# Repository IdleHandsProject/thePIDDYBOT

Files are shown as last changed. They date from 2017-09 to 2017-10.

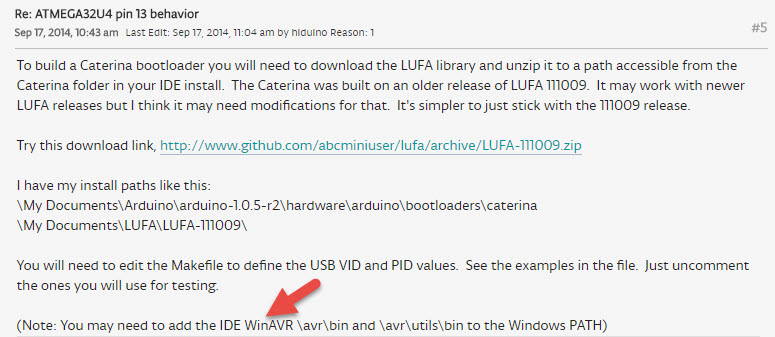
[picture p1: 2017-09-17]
PIDDYBOT_V1_32U4/bootloader/WinAVR.jpg

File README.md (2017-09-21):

# thePIDDYBOT
PIDDYBOT is an Open Source Balancing Robot with the aim of teaching PID control.

Check out the Video:

PIDDYBOT on YouTube (https://youtu.be/eyG5GFpSRSM)

Do not populate F1 or D6

**I somehow lost the original EagleCAD files for the PIDDYBOT. I still have the .BRD file, but no schem. I have plans to update the design with the SAMD21 instead of the Atmel, and it will be done in KiCad not Eagle. Stay Tuned**

There is an instructables on building the PIDDYBOT which contains the parts needed:
https://www.instructables.com/id/PIDDYBOT-DIY-Arduino-Balancing-Robot/

The FindChips(BOM):
https://www.findchips.com/org/10-open-hardware/list/46854-the-piddybot-encoders?sort=created&order=desc

HaD.io: https://hackaday.io/project/27330-the-piddybot

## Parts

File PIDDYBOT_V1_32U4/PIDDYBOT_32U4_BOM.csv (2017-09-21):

Digi-Key Part Number | Manufacturer | Manufacturer Part Number | Customer Reference | Quantity 1 | Quantity 2 | Quantity 3 | Mfg Std Lead Time | Description | Comments | RoHS Status | Lead Free Status | REACH Status
ATMEGA32U4-AURCT-ND | MICROCHIP TECHNOLOGY (VA) | ATMEGA32U4-AUR | U$1 | 1 | 0 | 0 | 14 Weeks | IC MCU 8BIT 32KB FLASH 44TQFP | Alternate Packaging Exists | RoHS Compliant | Lead free | Unaffected Jan-2017
609-3210-ND | AMPHENOL FCI | 67996-206HLF | JP5 | 1 | 0 | 0 | 8 Weeks | CONN HEADER 6POS .100 STR 15AU |  | RoHS Compliant | Lead free | Not Available
490-1459-1-ND | MURATA ELECTRONICS (VA) | GRM1885C1H222JA01D | C13 | 1 | 0 | 0 | 15 Weeks | CAP CER 2200PF 50V C0G/NP0 0603 | Alternate Packaging Exists | RoHS Compliant | Lead free | Unaffected Jun-2016
P1.0MGCT-ND | PANASONIC ELECTRONIC COMPONENTS (VA) | ERJ-3GEYJ105V | R1 | 1 | 0 | 0 | 43 Weeks | RES SMD 1M OHM 5% 1/10W 0603 | Alternate Packaging Exists | RoHS Compliant | Lead free | Unaffected Jan-2017
490-3297-1-ND | MURATA ELECTRONICS (VA) | GRM188R60J475KE19D | C3, C6 | 2 | 0 | 0 | 15 Weeks | CAP CER 4.7UF 6.3V X5R 0603 | Alternate Packaging Exists | RoHS Compliant | Lead free | Unaffected Jun-2016
740-1038-ND | MICROCHIP TECHNOLOGY | RN42-I/RM | U5 | 1 | 0 | 0 | 14 Weeks | RF TXRX MOD BLUETOOTH TRACE ANT | No delivery date available | RoHS Compliant | Lead free | Unaffected Jan-2017
490-1195-1-ND | MURATA ELECTRONICS (VA) | CSTCE8M00G55-R0 | Y1 | 1 | 0 | 0 | 9 Weeks | CER RES 8.0000MHZ 33PF SMD | Alternate Packaging Exists | RoHS Compliant | Lead free | Affected Jun-2016
311-2.00KHRCT-ND | YAGEO (VA) | RC0603FR-072KL | R4 | 1 | 0 | 0 | 16 Weeks | RES SMD 2K OHM 1% 1/10W 0603 | Alternate Packaging Exists | RoHS Compliant | Lead free | Unaffected Jan-2017
160-1446-1-ND | LITE-ON INC (VA) | LTST-C191KGKT | D1, D2 | 2 | 0 | 0 | 14 Weeks | LED GREEN CLEAR 0603 SMD | Alternate Packaging Exists | RoHS Compliant | Lead free | Unaffected Dec-2015
490-1512-1-ND | MURATA ELECTRONICS (VA) | GRM188R71H103KA01D | C16 | 1 | 0 | 0 | 39 Weeks | CAP CER 10000PF 50V X7R 0603 | Alternate Packaging Exists | RoHS Compliant | Lead free | Unaffected Jun-2016
576-1281-1-ND | MICROCHIP TECHNOLOGY (VA) | MIC5219-3.3YM5-TR | U6 | 1 | 0 | 0 | 7 Weeks | IC REG LINEAR 3.3V 500MA SOT23-5 | Alternate Packaging Exists | RoHS Compliant | Lead free | Unaffected Jan-2017
160-1447-1-ND | LITE-ON INC (VA) | LTST-C191KRKT | D11, D6 | 2 | 0 | 0 | 14 Weeks | LED RED CLEAR 0603 SMD | Alternate Packaging Exists | RoHS Compliant | Lead free | Unaffected Dec-2015
CKN9104CT-ND | C&K (VA) | PTS525SM15SMTR2 LFS | S1 | 1 | 0 | 0 | 16 Weeks | SWITCH TACTILE SPST-NO 0.02A 15V | Alternate Packaging Exists | RoHS Compliant | Lead free | Unaffected Jan-2017
1428-1007-1-ND | TDK INVENSENSE (VA) | MPU-6050 | U1 | 1 | 0 | 0 | 16 Weeks | IMU ACCEL/GYRO 3-AXIS I2C 24QFN | No delivery date available | RoHS Compliant | Lead free | Unaffected Jun-2016
MCP73831T-2ACI/OTCT-ND | MICROCHIP TECHNOLOGY (VA) | MCP73831T-2ACI/OT | U2 | 1 | 0 | 0 | 6 Weeks | IC CONTROLLR LI-ION 4.2V SOT23-5 | Alternate Packaging Exists | RoHS Compliant | Lead free | Unaffected Jan-2017
587-1242-1-ND | TAIYO YUDEN (VA) | LMK107B7105KA-T | C10, C22, C23 | 3 | 0 | 0 | 19 Weeks | CAP CER 1UF 10V X7R 0603 | Alternate Packaging Exists | RoHS Compliant | Lead free | Not Available
P3C3103-ND | PANASONIC ELECTRONIC COMPONENTS | EVU-F2AF30B14 | U$16,U$17,U$18 | 3 | 0 | 0 | 15 Weeks | POT 10K OHM 1/20W LINEAR |  | RoHS Compliant | Lead free | Not Available
160-1434-1-ND | LITE-ON INC (VA) | LTST-C190KFKT | D5,D3 | 2 | 0 | 0 | 14 Weeks | LED ORANGE CLEAR 0603 SMD | No delivery date available | RoHS Compliant | Lead free | Unaffected Dec-2015
609-4613-1-ND | AMPHENOL FCI (VA) | 10118192-0001LF | X2 | 1 | 0 | 0 | 12 Weeks | CONN USB MICRO B RECPT SMT R/A | Alternate Packaging Exists | RoHS Compliant | Lead free | Not Available
A100043-ND | TE CONNECTIVITY AMP | 440055-2 | CN2 | 1 | 0 | 0 | 13 Weeks | CONN HEADER 2POS R/A 2MM T/H |  | RoHS Compliant | Lead free | Not Available
455-1792-1-ND | JST SALES AMERICA INC (VA) | BM06B-SRSS-TB(LF)(SN) | JP3,JP4 | 2 | 0 | 0 | 14 Weeks | CONN HEADER SH 6POS TOP 1MM TIN | Alternate Packaging Exists | RoHS Compliant | Lead free | Not Available
311-1343-1-ND | YAGEO (VA) | CC0603ZRY5V9BB104 | C9, C11, C12, C14, C17, C18,C8 | 7 | 0 | 0 | 16 Weeks | CAP CER 0.1UF 50V Y5V 0603 | Alternate Packaging Exists | RoHS Compliant | Lead free | Unaffected Jan-2017
311-1.0KGRCT-ND | YAGEO (VA) | RC0603JR-071KL | R5,R2, R7, R8, R12, R21 | 6 | 0 | 0 | 16 Weeks | RES SMD 1K OHM 5% 1/10W 0603 | Alternate Packaging Exists | RoHS Compliant | Lead free | Unaffected Jan-2017
311-10KGRCT-ND | YAGEO (VA) | RC0603JR-0710KL | R6, R22, R10, R11 | 4 | 0 | 0 | 16 Weeks | RES SMD 10K OHM 5% 1/10W 0603 | Alternate Packaging Exists | RoHS Compliant | Lead free | Unaffected Jan-2017
609-3461-ND | AMPHENOL FCI | 68000-103HLF | S4 | 1 | 0 | 0 | 8 Weeks | BERGSTIK II .100" SR STRAIGHT |  | RoHS Compliant | Lead free | Not Available
P0.0JCT-ND | PANASONIC ELECTRONIC COMPONENTS (VA) | ERJ-2GE0R00X | L2 | 1 | 0 | 0 | 43 Weeks | RES SMD 0 OHM JUMPER 1/10W 0402 | Alternate Packaging Exists | RoHS Compliant | Lead free | Unaffected Jun-2016
296-30391-1-ND | TEXAS INSTRUMENTS (VA) | DRV8835DSSR | U$2 | 1 | 0 | 0 | 10 Weeks | IC MOTOR DRIVER PAR 12WSON | Alternate Packaging Exists | RoHS Compliant | Lead free | Unaffected Jun-2016
311-1376-1-ND | YAGEO (VA) | CC1206ZKY5V7BB106 | C7,C15, C5 | 3 | 0 | 0 | 15 Weeks | CAP CER 10UF 16V Y5V 1206 | Alternate Packaging Exists | RoHS Compliant | Lead free | Unaffected Jan-2017
311-22GRCT-ND | YAGEO (VA) | RC0603JR-0722RL | R9, R13 | 2 | 0 | 0 | 16 Weeks | RES SMD 22 OHM 5% 1/10W 0603 | Alternate Packaging Exists | RoHS Compliant | Lead free | Unaffected Jan-2017
311-470KGRCT-ND | YAGEO (VA) | RC0603JR-07470KL | R3 | 1 | 0 | 0 | 16 Weeks | RES SMD 470K OHM 5% 1/10W 0603 | Alternate Packaging Exists | RoHS Compliant | Lead free | Unaffected Jan-2017

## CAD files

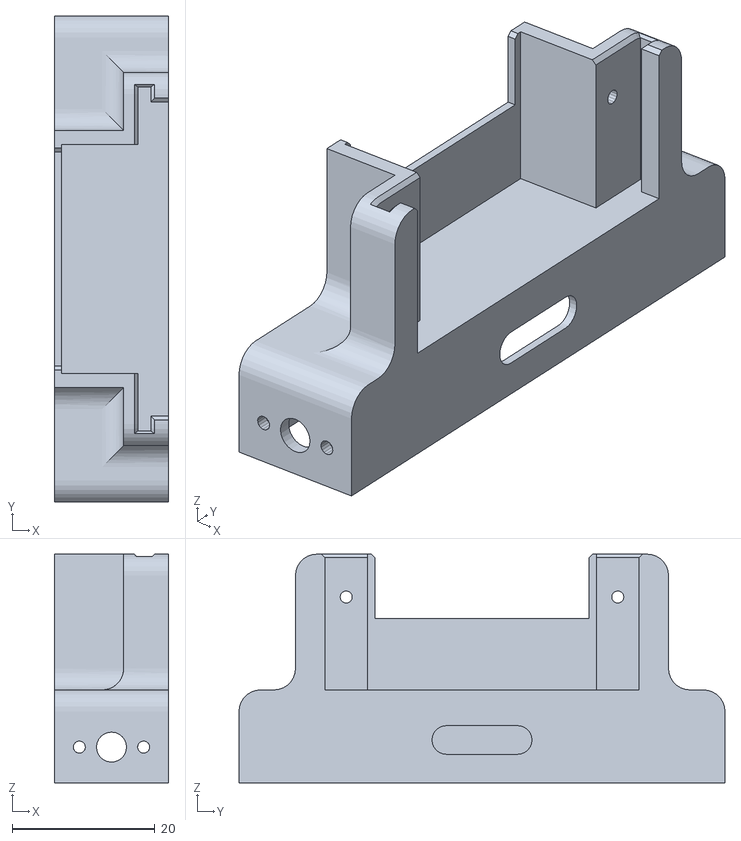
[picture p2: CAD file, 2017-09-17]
body/PIDDYBody_small_motor_lightweight.stl
16.0 x 68.0 x 32.0

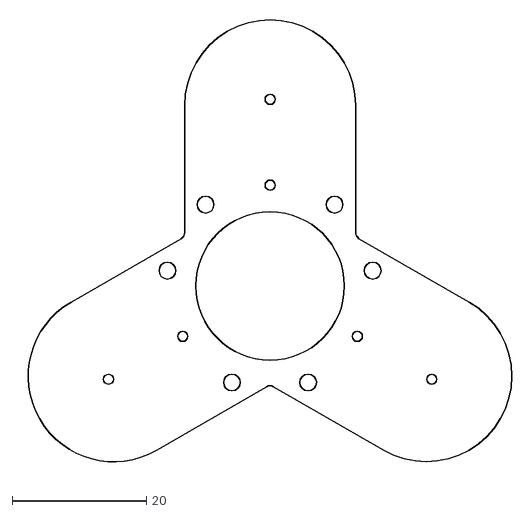
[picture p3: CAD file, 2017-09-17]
latch_encoder/PCB/Body.dxf
73.8 x 68.1

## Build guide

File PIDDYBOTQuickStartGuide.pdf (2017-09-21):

# PIDDYBOT Quick Start Guide

## For PIDDYBOT_32U4_V11 Firmware

Idle Hands Development

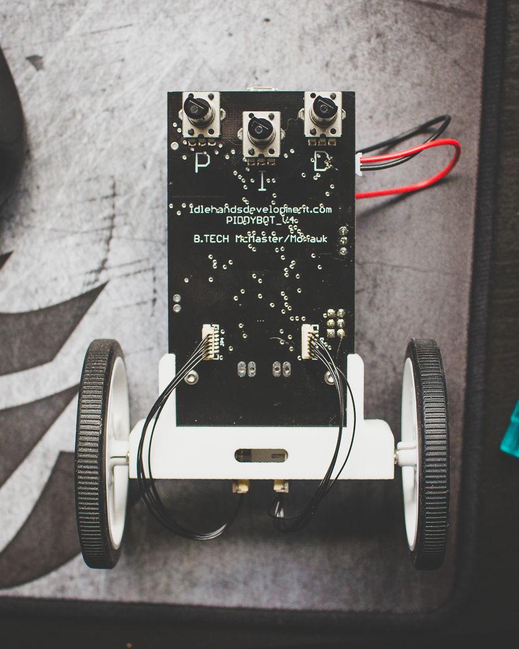
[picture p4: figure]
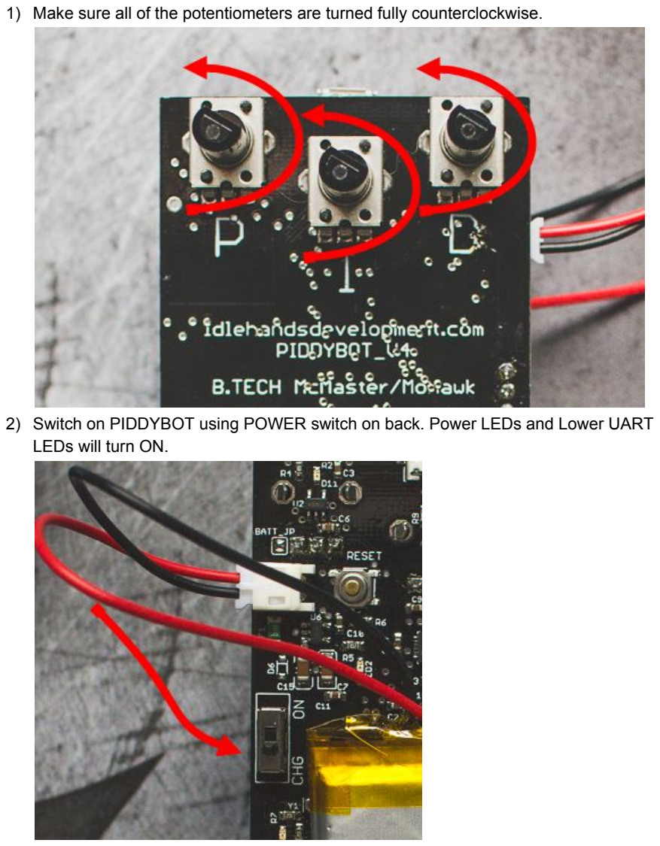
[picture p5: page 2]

1) Make sure all of the potentiometers are turned fully counterclockwise.
2) Switch on PIDDYBOT using POWER switch on back. Power LEDs and Lower UART LEDs will turn ON.

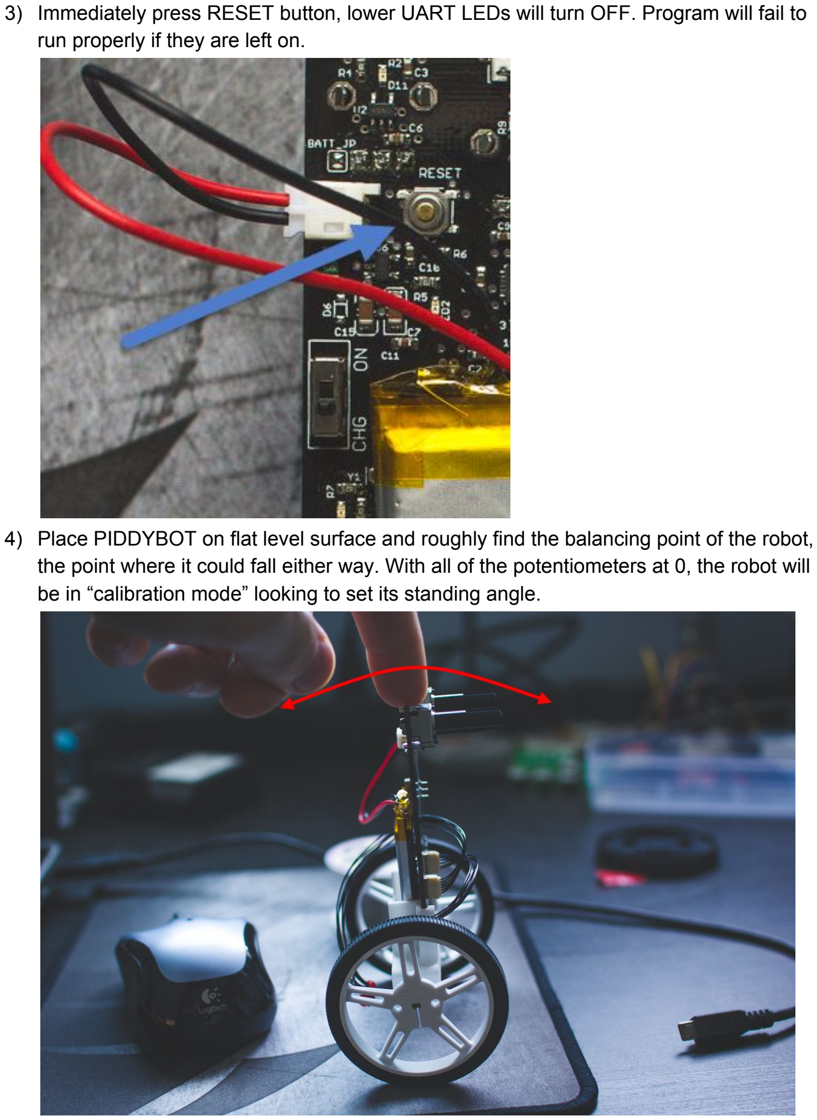
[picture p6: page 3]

3) Immediately press RESET button, lower UART LEDs will turn OFF. Program will fail to run properly if they are left on.
4) Place PIDDYBOT on flat level surface and roughly find the balancing point of the robot, the point where it could fall either way. With all of the potentiometers at 0, the robot will be in “calibration mode” looking to set its standing angle.

5) Hold the PIDDYBOT in the balancing position and slowly turn the P term knob up. Doing so will take the Robot out of “Calibration Mode” and set the angle it will use to balance. Turning any of the knobs out of zero(fully counter clockwise) will take the robot out of “Calibration Mode” - and the opposite, if you need to change the angle because it is not correct, set all of the knobs back to zero.

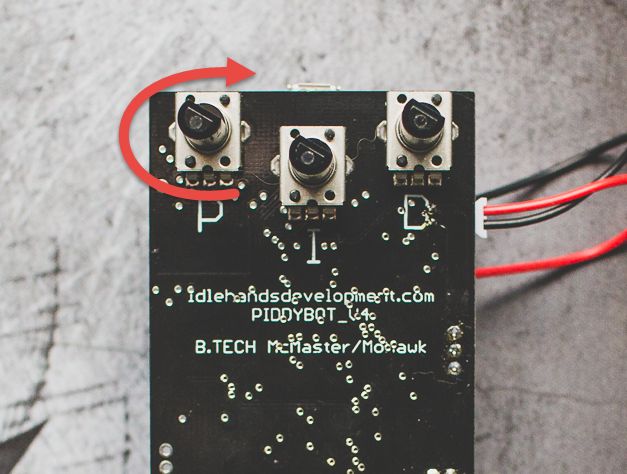
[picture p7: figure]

6) You may now try and tune the PID terms to see the different effects it has on the system.

The Robot will save the last calibration angle for when you restart it. However, every time all of the knobs are turned to zero while the PIDDYBOT is powered ON, it will reset this angle to a new one.

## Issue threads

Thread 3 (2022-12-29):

No schematic or wiring diagram

kyle-kelly, 2022-12-29:
There is no schematic or wiring diagram to aid in the assembly. Could you please provide one or both?

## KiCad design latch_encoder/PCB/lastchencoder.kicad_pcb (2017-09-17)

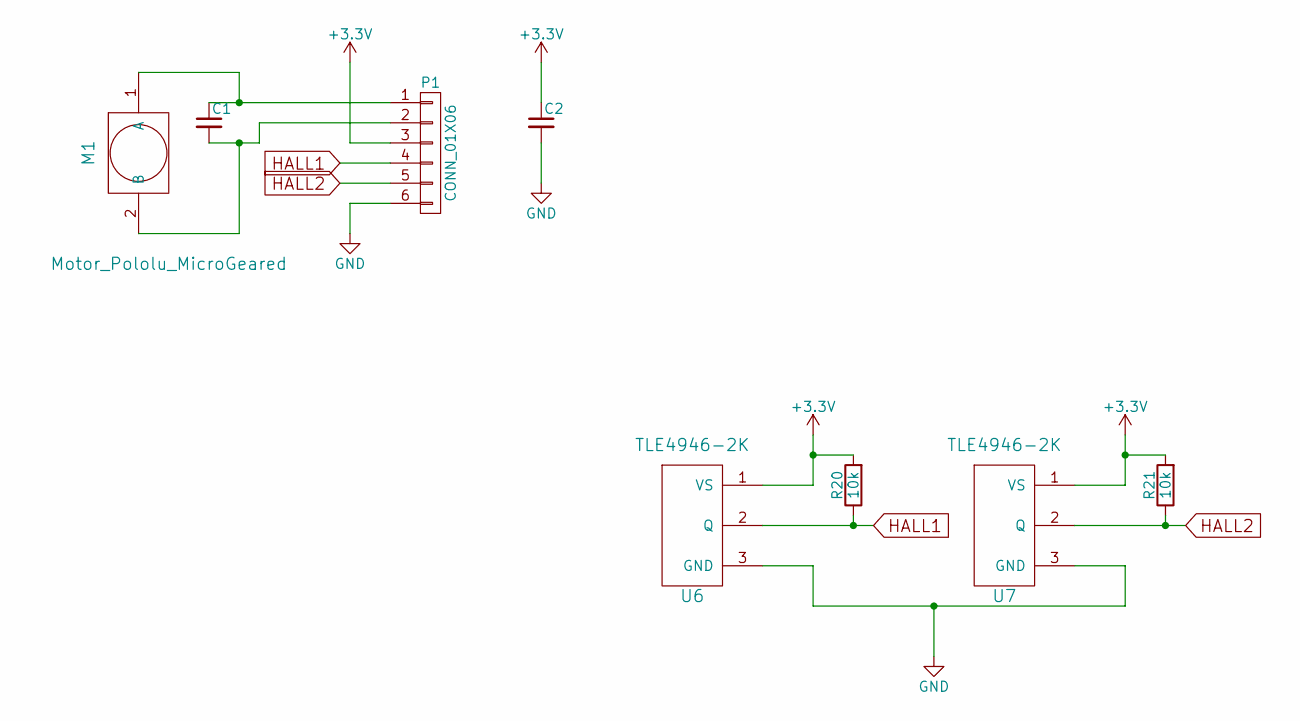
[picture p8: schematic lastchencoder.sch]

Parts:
C1: 3.3nF; C_0402_Hand; Digikey Part No. 1276-1549-1-ND
C2: 0.1uF; C_0402_Hand; Digikey Part No. 490-6328-1-ND
M1: Motor_Pololu_MicroGeared; motor_pololu_microgeared
P1: CONN_01X06; Connectors_JST_SM06B-SRSS-TB
R20, R21: 10k; R_0402_Hand; Digikey Part No. 311-10KJRCT-ND
U6, U7: TLE4946-2K; SOT23; Digikey Part No. TLE49462KHTSA1CT-ND

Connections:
+3V3: C2.1, P1.3, R20.2, R21.2, U6.1 (VS), U7.1 (VS)
GND: C2.2, P1.6, U6.3 (GND), U7.3 (GND)
HALL1: P1.4, R20.1, U6.2 (Q)
HALL2: P1.5, R21.1, U7.2 (Q)
unnamed: C1.1, M1.1 (A), P1.1
unnamed: C1.2, M1.2 (B), P1.2

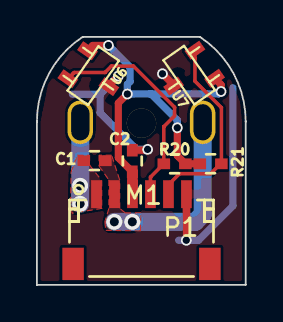
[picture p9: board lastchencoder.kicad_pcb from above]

Board: 2 copper layers, 11.6 x 13.8 mm, 8 parts (0 on the bottom side), 6 nets.

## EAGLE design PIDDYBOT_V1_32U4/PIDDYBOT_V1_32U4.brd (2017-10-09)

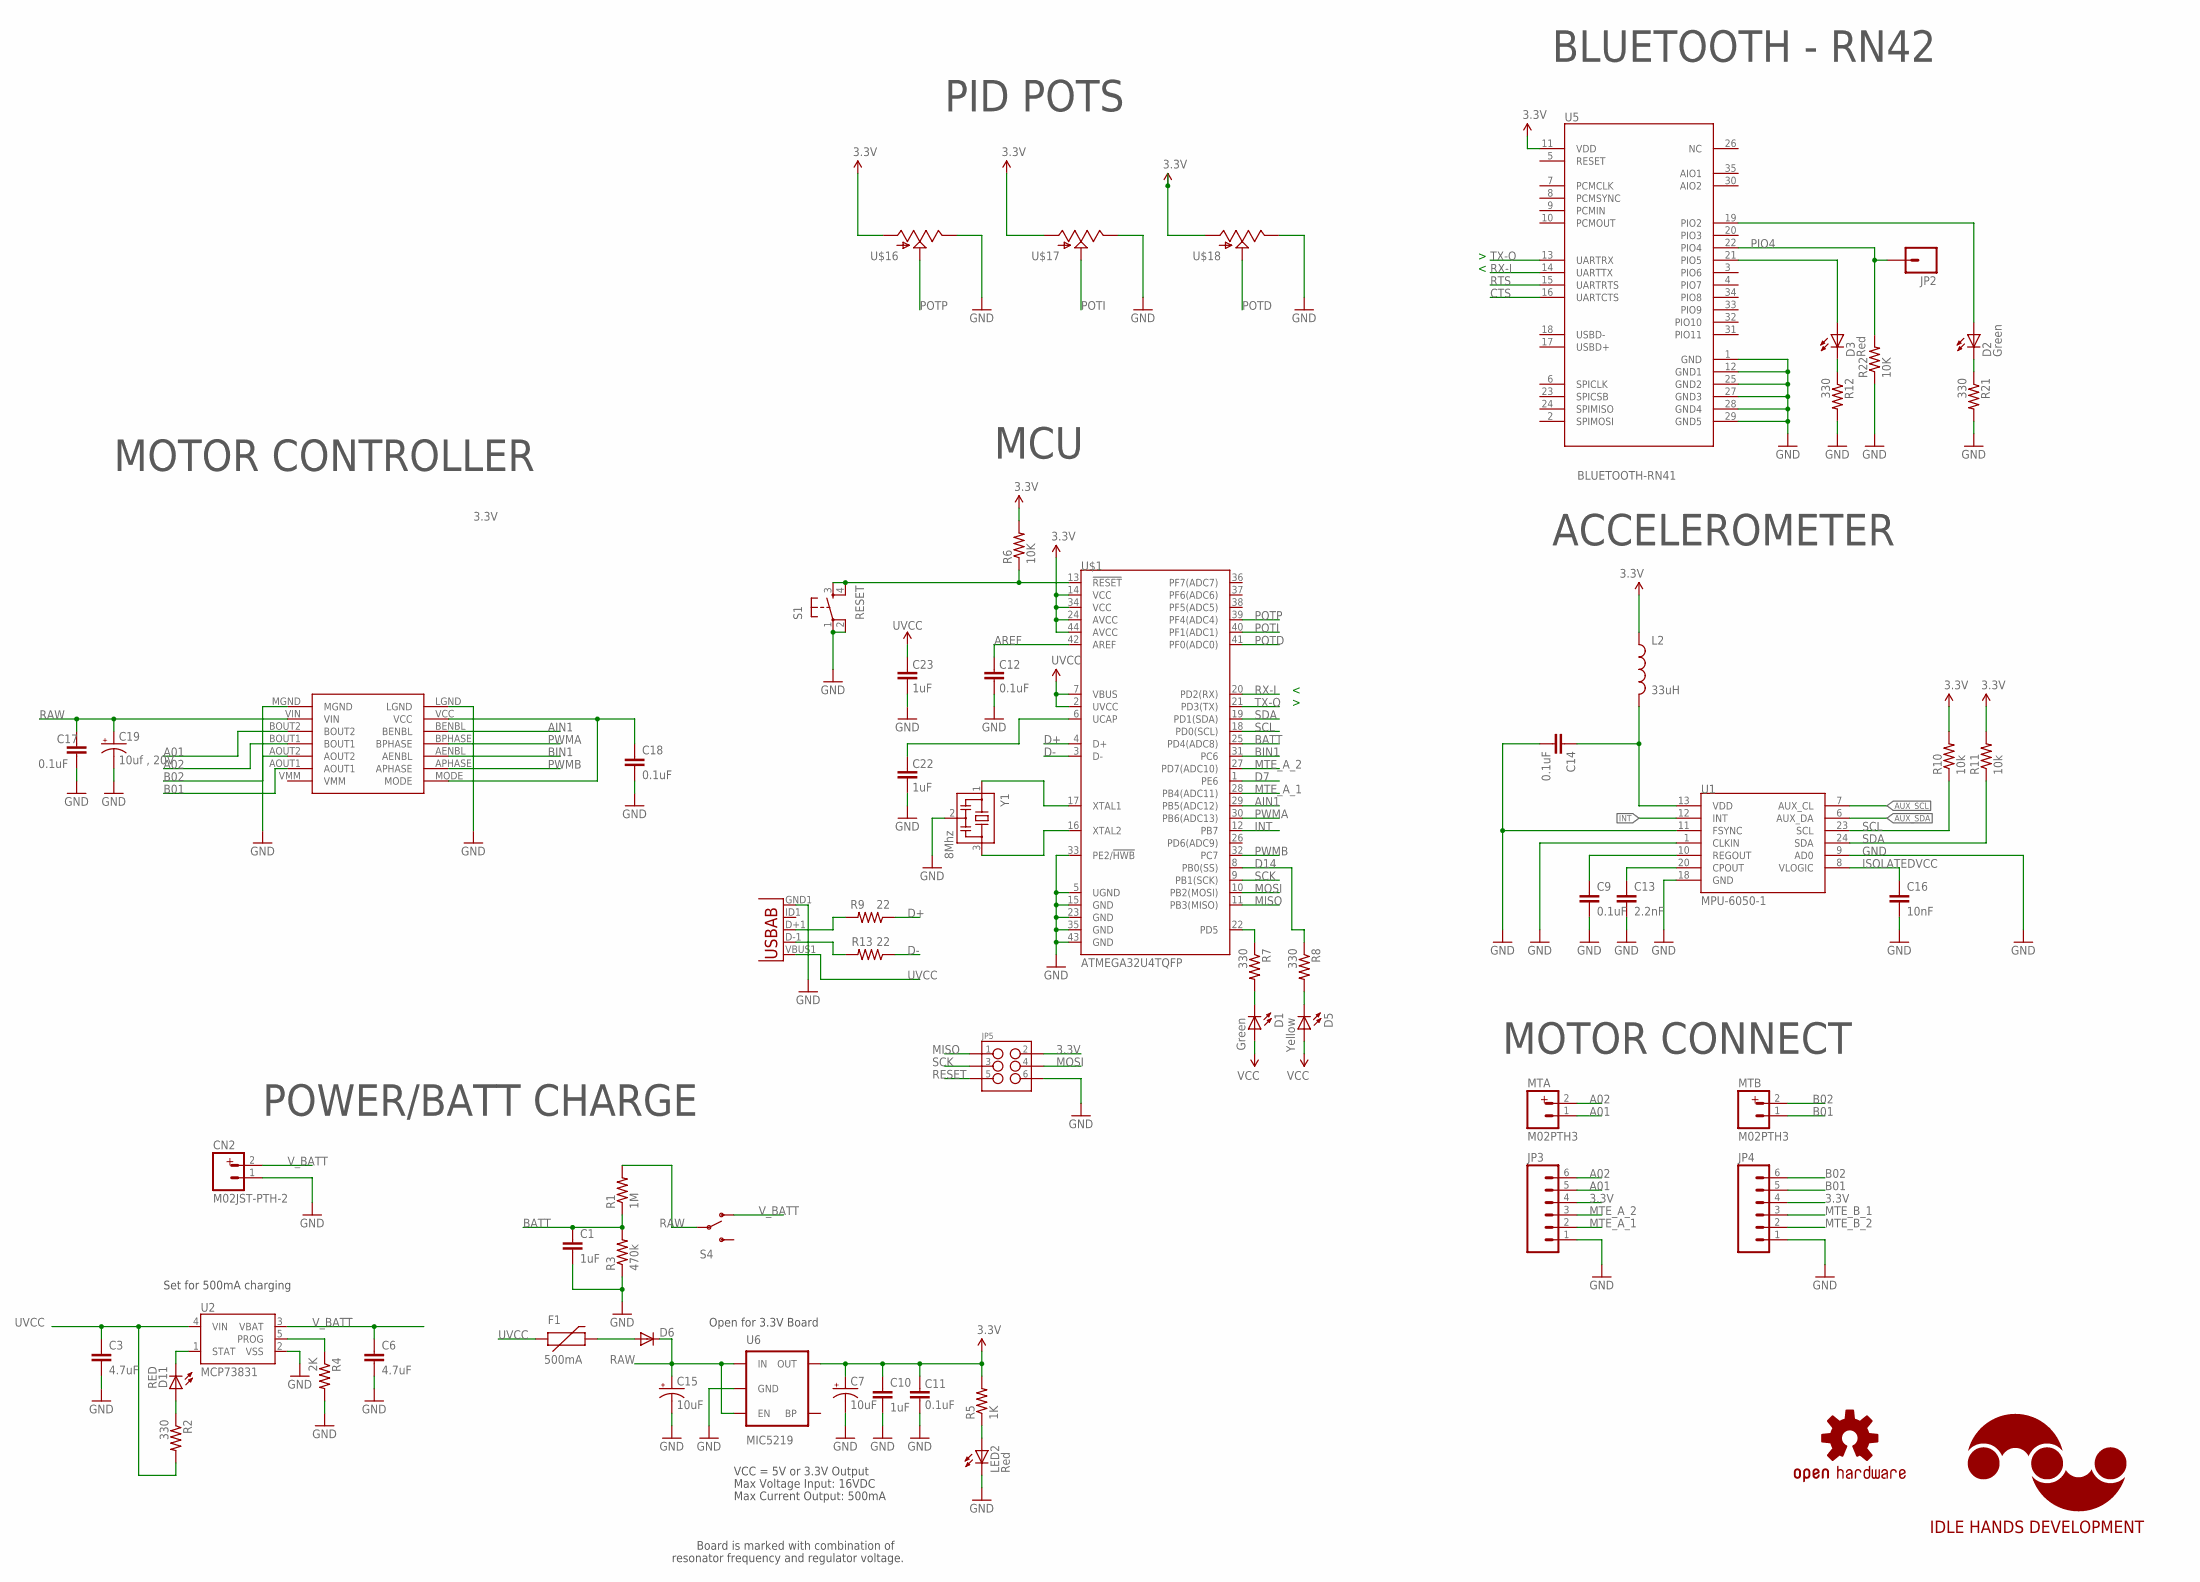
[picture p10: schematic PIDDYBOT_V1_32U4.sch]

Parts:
C1, C10, C22, C23: 1uF; 0603-CAP
C3, C6: 4.7uF; 0603-CAP
C7, C15: 10uF; EIA3216
C9, C11, C12, C14, C17, C18: 0.1uF; 0603-CAP
C13: 2.2nF; 0603-CAP
C16: 10nF; 0603-CAP
C19: 10uf , 20V; EIA3528
CN2: M02JST-PTH-2; JST-2-PTH
D1, D2: Green; LED-0603
D3: Red; LED-0603
D5: Yellow; LED-0603
D6: DIODESOD; SOD-323
D11: RED; LED-0603
F1: 500mA; PTC-1206
JP2: M01SMDNS; 1X01NS
JP3, JP4: M06SMD-1MM; 1X06-1MM
JP5: M03X2NO_SILK; 2X3-NS
L2: 33uH; C0402
LED2: Red; LED-0603
LOGO1: IDLEHANDS_LOGOL; IHD-LOGO-L
LOGO2: OSHW-LOGOM; OSHW-LOGO-M
MTA: M02PTH3; 1X02_LONGPADS
MTB: M02PTH3; 1X02_LONGPADS
R1: 1M; 0603-RES
R2, R7, R8, R12, R21: 330; 0603-RES
R3: 470k; 0603-RES
R4: 2K; 0603-RES
R5: 1K; 0603-RES
R6, R22: 10K; 0603-RES
R9, R13: 22; 0603-RES
R10, R11: 10k; 0603-RES
S1: RESET; TACTILE_SWITCH_SMD
S4: SWITCH-SPDTPTH; SWITCH-SPDT
U1: MPU-6050-1; QFN-24-4MM2
U2: MCP73831; SOT23-5
U5: BLUETOOTH-RN41; RN41
U6: MIC5219; SOT23-5
U$1: ATMEGA32U4TQFP; SPARKFUN-DIGITALIC_TQFP44
U$2: POLOLU_MOTOR_DRV8835THROUGHHOLE; POLOLU_MOTOR_DRV_DRV8835
U$16, U$17, U$18: POT; ALPS_POT
X2: USB-ABIN&OUT; USB-AB-MICRO-SMD-V03-IN&OUT
Y1: 8Mhz; CSTCR6M

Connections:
3.3V: C7.A (+), C10.1, C11.2, C18.1, D1.A, D5.A, JP3.4, JP4.4, JP5.2, L2.1, R5.2, R6.2, R10.2, R11.2, U5.11 (VDD), U6.5 (OUT), U$1.14 (VCC), U$1.24 (AVCC), U$1.34 (VCC), U$1.44 (AVCC), U$2.MODE, U$16.P$3 (A), U$17.P$3 (A), U$18.P$3 (A)
A01: JP3.5, MTA.1, U$2.BOUT2
A02: JP3.6, MTA.2, U$2.BOUT1
AIN1: U$1.29 (PB5(ADC12)), U$2.BENBL
AREF: C12.2, U$1.42 (AREF)
AUX_SCL: U1.7 (AUX_CL)
AUX_SDA: U1.6 (AUX_DA)
B01: JP4.5, MTB.1, U$2.AOUT1
B02: JP4.6, MTB.2, U$2.AOUT2
BATT: C1.1, R1.1, R3.2, U$1.25 (PD4(ADC8))
BIN1: U$1.31 (PC6), U$2.AENBL
CTS: U5.16 (UARTCTS)
D1: D3.C, R12.1
D2: D2.C, R21.1
D7: U$1.1 (PE6)
D14: R8.1, U$1.8 (PB0(SS))
D+: R9.1, U$1.4 (D+)
D-: R13.1, U$1.3 (D-)
GND: C1.2, C3.2, C6.2, C7.C (-), C9.2, C10.2, C11.1, C12.1, C13.2, C14.2, C15.C (-), C16.2, C17.2, C18.2, C19.C (-), C22.1, C23.1, CN2.1, JP3.1, JP4.1, JP5.6, LED2.C, R3.1, R4.2, R12.2, R21.2, R22.1, S1.1, S1.2, U1.1 (CLKIN), U1.9 (AD0), U1.11 (FSYNC), U1.18 (GND), U2.2 (VSS), U5.1 (GND), U5.12 (GND1), U5.25 (GND2), U5.27 (GND3), U5.28 (GND4), U5.29 (GND5), U6.2 (GND), U$1.5 (UGND), U$1.15 (GND), U$1.23 (GND), U$1.33 (PE2/!HWB), U$1.35 (GND), U$1.43 (GND), U$2.LGND, U$2.MGND, U$16.P$1 (E), U$17.P$1 (E), U$18.P$1 (E), X2.GND1 (GND), Y1.2
INT: U1.12 (INT), U$1.12 (PB7)
ISOLATEDVCC: C14.1, C16.1, L2.2, U1.8 (VLOGIC), U1.13 (VDD)
MISO: JP5.1, U$1.11 (PB3(MISO))
MOSI: JP5.4, U$1.10 (PB2(MOSI))
MTE_A_1: JP3.2, U$1.28 (PB4(ADC11))
MTE_A_2: JP3.3, U$1.27 (PD7(ADC10))
MTE_B_1: JP4.3
MTE_B_2: JP4.2
unnamed: U$1.17 (XTAL1), Y1.1
unnamed: U$1.16 (XTAL2), Y1.3
unnamed: D6.2 (A), F1.2
unnamed: C13.1, U1.20 (CPOUT)
unnamed: C9.1, U1.10 (REGOUT)
unnamed: D3.A, U5.21 (PIO5)
unnamed: D2.A, U5.19 (PIO2)
unnamed: D11.A, R2.1
unnamed: C22.2, U$1.6 (UCAP)
unnamed: R13.2, X2.D-1 (D-)
unnamed: R9.2, X2.D+1 (D+)
unnamed: D5.C, R8.2
unnamed: D1.C, R7.2
unnamed: LED2.A, R5.1
PIO4: JP2.1, R22.2, U5.22 (PIO4)
POTD: U$1.41 (PF0(ADC0)), U$18.P$2 (S)
POTI: U$1.40 (PF1(ADC1)), U$17.P$2 (S)
POTP: U$1.39 (PF4(ADC4)), U$16.P$2 (S)
PROG: R4.1, U2.5 (PROG)
PWMA: U$1.30 (PB6(ADC13)), U$2.BPHASE
PWMB: U$1.32 (PC7), U$2.APHASE
RAW: C15.A (+), C17.1, C19.A (+), D6.1 (C), R1.2, S4.2, U6.1 (IN), U6.3 (EN), U$2.VIN
RESET: JP5.5, R6.1, S1.3, S1.4, U$1.13 (!RESET)
RTS: U5.15 (UARTRTS)
RX-I: U5.14 (UARTTX), U$1.20 (PD2(RX))
SCK: JP5.3, U$1.9 (PB1(SCK))
SCL: R10.1, U1.23 (SCL), U$1.18 (PD0(SCL))
SDA: R11.1, U1.24 (SDA), U$1.19 (PD1(SDA))
STAT: D11.C, U2.1 (STAT)
TX-O: U5.13 (UARTRX), U$1.21 (PD3(TX))
TXLED: R7.1, U$1.22 (PD5)
UVCC: C3.1, C23.2, F1.1, R2.2, U2.4 (VIN), U$1.2 (UVCC), U$1.7 (VBUS), X2.VBUS1 (VBUS)
V_BATT: C6.1, CN2.2, S4.1 (O), U2.3 (VBAT)

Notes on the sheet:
Set for 500mA charging
Max Voltage Input: 16VDC
Max Current Output: 500mA
Board is marked with combination of
resonator frequency and regulator voltage.
VCC = 5V or 3.3V Output
Open for 3.3V Board
MOTOR CONTROLLER
MCU
PID POTS
BLUETOOTH - RN42
ACCELEROMETER
MOTOR CONNECT
POWER/BATT CHARGE

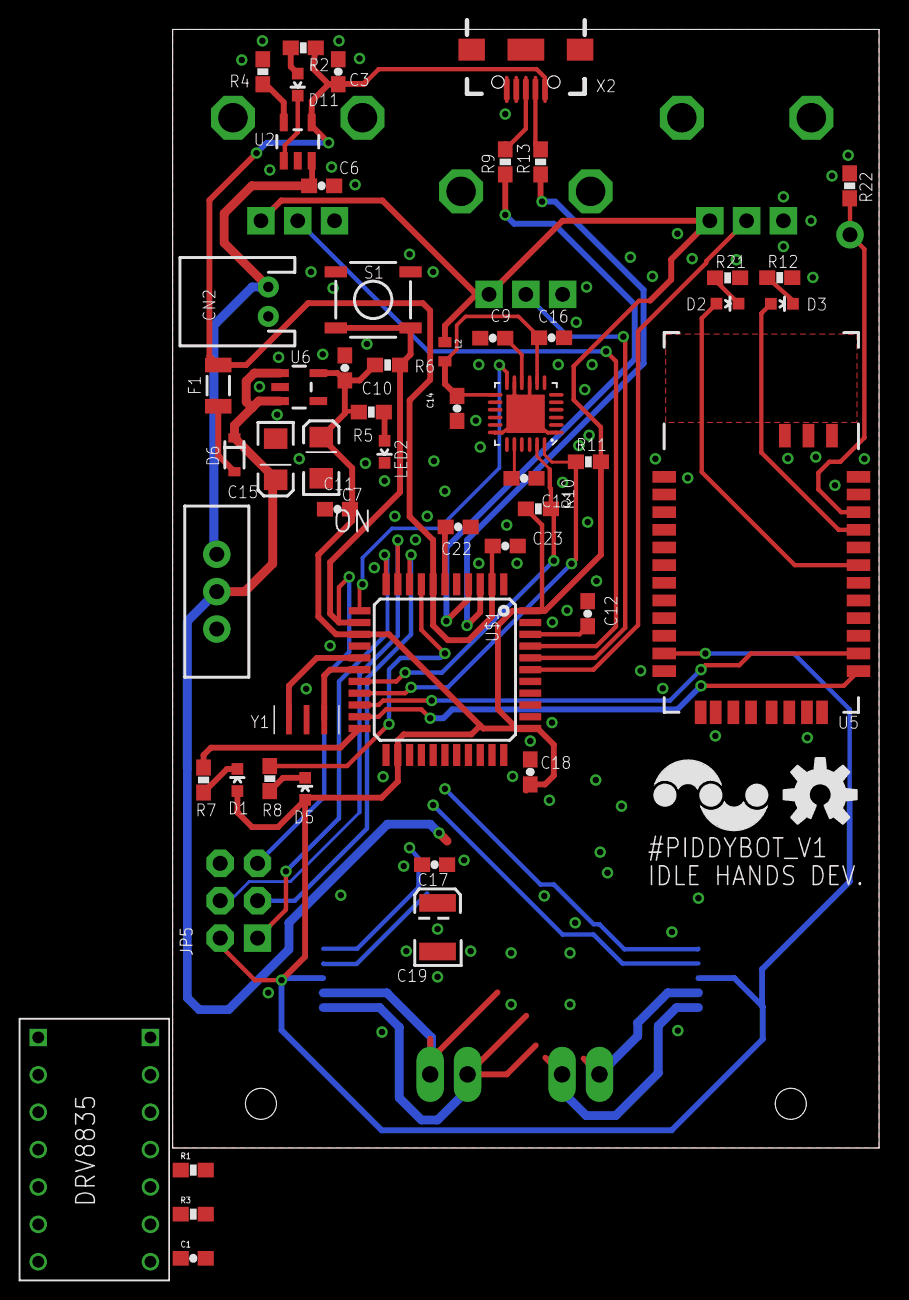
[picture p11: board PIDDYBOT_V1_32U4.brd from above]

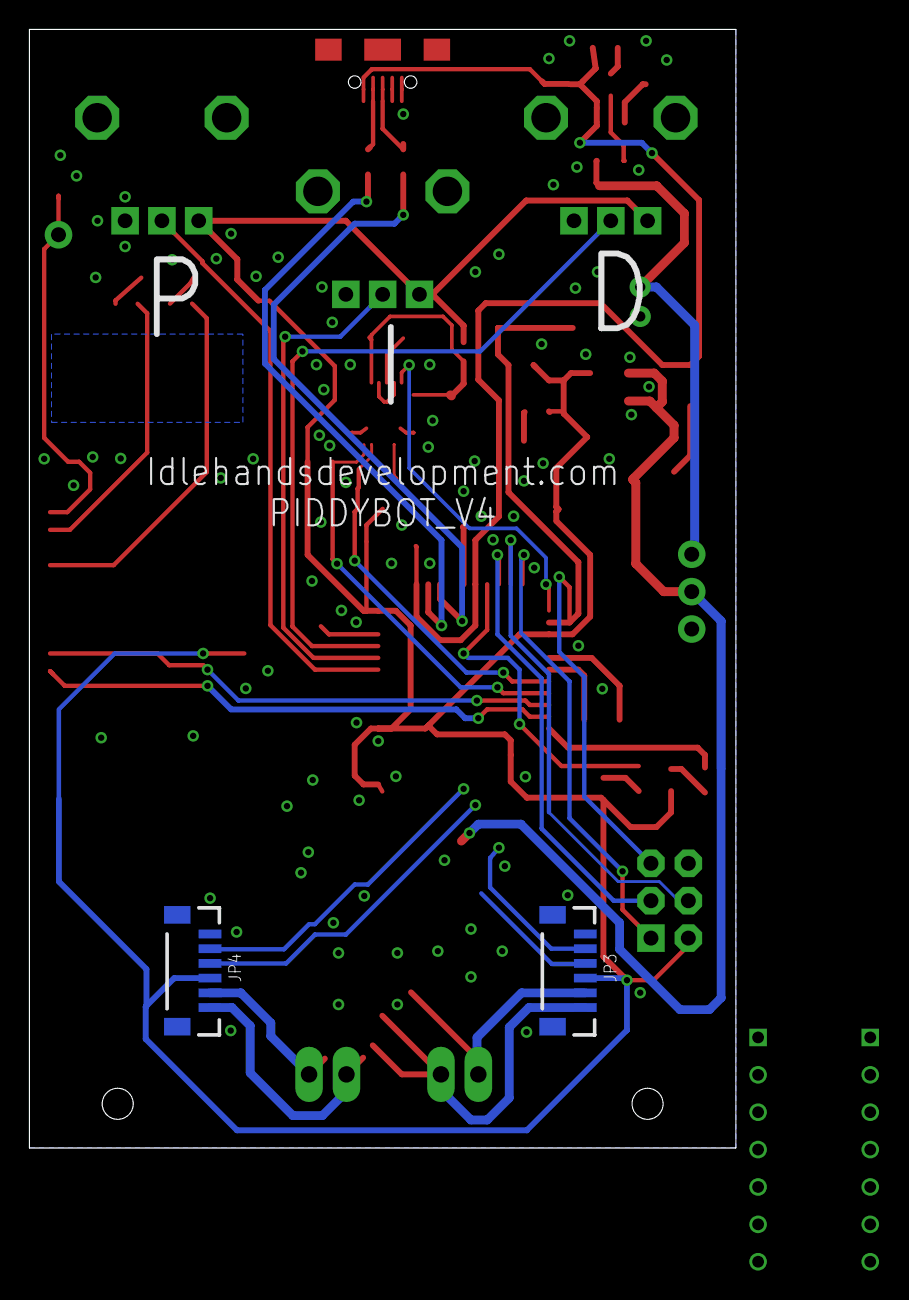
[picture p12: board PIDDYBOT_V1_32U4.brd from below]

Board: 2 copper layers, 48.0 x 76.0 mm, 63 parts (5 on the bottom side), 53 nets.

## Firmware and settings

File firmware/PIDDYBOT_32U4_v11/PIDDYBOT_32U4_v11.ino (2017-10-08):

//USE WITH THE SINGLE BOARD PIDDYBOT(Complete PCB)
// Latest Version of PIDDYBOT Self Balancing Program 08/10/17
// Program created by Sean Hodgins.
// Http://Idlehandsproject.com
// This is free to be shared, altered, and used.
// LIBRARIES
//For use with board Version 1.1 - ATMEGA32U4 with DRV8835 Motor Driver


//#define DEBUG_ENABLE
//#define HARD_PID_VALUES
//#define EPID_TUNE
//#define RAW_ACC
//#define BT_CONN
#define BT_GRAPHS
#include <Wire.h>

#include "Kalman.h"
#include <MPU6050.h>
#include <I2Cdev.h>

#include <EEPROM.h>

#include <Encoder.h>

int A = 1;
int B = 2;

//Motor A
int PWMA = 10; //Speed control
int AIN1 = 9; //Direction

//Motor B
int PWMB = 13; //Speed control
int BIN1 = 5; //Direction

// Potentiometers
static int pot1 = A3;
static int pot2 = A4;
static int pot3 = A5;

static int BATT = A6;

//float distancecount = 0;
float correction = -10;
int correctionEn = 1;
int returnto = 0;

int moveDir = 1;

#define RESTRICT_PITCH


//int drive = 0;

// PID CONSTANTS
float Kp = 0;
float Ki = 0;
float Kd = 0;

// from MPU datasheet
//const float accScale = 8192;
//const float gyroScale = 131;

//const int numGyroSamples = 300;

//const float gyroWeight = .90;
//const float accWeight = .10;

double accX, accY, accZ;
double gyroX, gyroY, gyroZ;
int16_t tempRaw;

Kalman kalmanX; // Create the Kalman instances
//Kalman kalmanY;

double gyroXangle;//, gyroYangle; // Angle calculate using the gyro only
double compAngleX;//, compAngleY; // Calculated angle using a complementary filter
double kalAngleX;//, kalAngleY;

uint32_t timer;
uint8_t i2cData[14];
int16_t ax, ay, az;
int16_t gx, gy, gz;

MPU6050 mpu;

float gyroOffset = 0; // set in calibrateGyro()

const int AvgAngles = 3;
float prevTargetAngle = 0;
float targetAngle = -90;
uint8_t saveAngle = 0;
int tAngle = 0;


float angles[5];

float currAngle = 0;
float prevAngle = 0;
float prevAngles[AvgAngles];
int prevAngleI = 0;
int motorSpeed;
float rotate = 1;
int forward = 0;
int coursetiming = 0;
int dir = 0;
int lastdir = 0;

float errorSum = 0;
float currError = 0;
float prevError = 0;
float iTerm = 0;
float dTerm = 0;
float pTerm = 0;

//Location PID CONTROL - These are the PID control for the robot trying to hold its location.
float Lp = 1;
float Li = 0;
float Ld = 0;
float offsetLoc = 0;
float pT, iT, dT = 0;
float errorS = 0;
float prevE = 0;
float mSpeed = 0;
float Movement = 0;

int turnREn = 0;
int turnLEn = 0;

int fallflag = 0;

unsigned long previousBTTime = 0;


const long BTinterval = 1000;
////////////NEW ENCODER////////////////
//#define A_ENC 12
//#define B_ENC
//Encoder myEncA(14, 12);
Encoder myEncB(8, 6);
void pin3func() {
  //  returnto = myEncA.read();

  returnto = constrain(returnto, -5000, 5000);

}
/////////////NEW ENCODER////////////////

void setup() {
  //MOTOR SETUP
  pinMode(PWMA, OUTPUT);
  pinMode(AIN1, OUTPUT);
  pinMode(PWMB, OUTPUT);
  pinMode(BIN1, OUTPUT);
  pinMode(BATT, INPUT);

  // Serial Connection
  Serial.begin(38400);
  Serial1.begin(115200);
  Serial1.flush();
  //while(!Serial1);
  //while(!Serial);
  // IMU Connection
  Wire.begin();

  delay(5);
  mpu.initialize();

  // Testing MPU
#ifdef RESTRICT_PITCH
  Serial1.println(mpu.testConnection() ? "MPU is good!" : "Oops! Check the connections");
#endif

  KalmanInit();

  //  myEncA.write(0);
  myEncB.write(0);
  checkBatt();
  saveAngle = EEPROM.read(1);
  tAngle = saveAngle * -1;
}


void loop() {


  //testMotors();
  checkBatt();
  checkPots();


#ifdef EPID_TUNE
  PIDtune();
#else
  Lp = 0.05;
  Ld = 0.0;
#endif

  updateLocation();
  targetAngle = tAngle + correction;// + (correction * correctionEn * 1);
  //Serial.println(targetAngle);
  updateAngle();
  //Serial.print(targetAngle);
  //Serial.print("\t");
  //Serial.println(currAngle);



#ifdef DEBUG_ENABLE
  //Serial.print("P term: ");
  //Serial.print(Kp);
  //Serial.print("I term: ");
  //Serial.print(Ki);
  //Serial.print("D term: ");
  //Serial.println(Kd);

  Serial.print(currAngle);
  Serial.print(",");
  Serial.print("0");
  Serial.print(",");
  Serial.print("0");
  Serial.print(",");
  Serial.println("0");
#else
#endif



#ifdef HARD_PID_VALUES ///Makes the PID POTs do nothing!Hard values 
  Kp = 7.5;
  Ki = 0.1;
  Kd = 40;
#else
  Kp = map(analogRead(pot1), 0, 1023, 0, 1000);  //Tuning Pots for P I and D term.
  Ki = map(analogRead(pot2), 0, 1023, 0, 100);
  Kd = map(analogRead(pot3), 0, 1023, 0, 5000);
  Kp = Kp / 100;
  Ki = Ki / 100;
  Kd = Kd / 100;
#endif

  updateSpeed();
  updateMotor();

#ifdef BT_GRAPHS
  unsigned long currentBTTime = millis();

  if (currentBTTime - previousBTTime >= 10) {
    // save the last time you blinked the LED
    previousBTTime = currentBTTime;
    Serial1.print("E");
    Serial1.print(currAngle);
    Serial1.print(",");
    Serial1.print(motorSpeed);
    Serial1.print('\n');
  }
#endif



}

//Subroutine for finding new angle and using Kalman Filter.
void updateAngle() {

  while (i2cRead(0x3B, i2cData, 14));
  accX = ((i2cData[0] << 8) | i2cData[1]);
  accY = ((i2cData[2] << 8) | i2cData[3]);
  accZ = ((i2cData[4] << 8) | i2cData[5]);
  tempRaw = (i2cData[6] << 8) | i2cData[7];
  gyroX = (i2cData[8] << 8) | i2cData[9];
  gyroY = (i2cData[10] << 8) | i2cData[11];
  gyroZ = (i2cData[12] << 8) | i2cData[13];

  double dt = (double)(micros() - timer) / 1000000; // Calculate delta time
  timer = micros();

#ifdef RAW_ACC
  Serial.print("Ax: ");
  Serial.print(accX);
  Serial.print("Ay: ");
  Serial.print(accY);
  Serial.print("Az: ");
  Serial.println(accZ);
  Serial.print("Gx: ");
  Serial.print(gyroX);
  Serial.print("Gy: ");
  Serial.print(gyroY);
  Serial.print("Gz: ");
  Serial.println(gyroZ);
#endif
#ifdef RESTRICT_PITCH // Eq. 25 and 26
  double roll  = atan2(accY, accZ) * RAD_TO_DEG;
  //double pitch = atan(-accX / sqrt(accY * accY + accZ * accZ)) * RAD_TO_DEG;
#endif

  double gyroXrate = gyroX / 131.0; // Convert to deg/s
  //double gyroXrate = gyroX / 16.4;

#ifdef RESTRICT_PITCH
  // This fixes the transition problem when the accelerometer angle jumps between -180 and 180 degrees
  if ((roll < -90 && kalAngleX > 90) || (roll > 90 && kalAngleX < -90)) {
    kalmanX.setAngle(roll);
    compAngleX = roll;
    kalAngleX = roll;
    gyroXangle = roll;
  }
  else
    kalAngleX = kalmanX.getAngle(roll, gyroXrate, dt); // Calculate the angle using a Kalman filter
#endif

  gyroXangle += gyroXrate * dt; // Calculate gyro angle without any filter


  compAngleX = 0.99 * (compAngleX + gyroXrate * dt) + 0.01 * roll; // Calculate the angle using a Complimentary filter


  // Reset the gyro angle when it has drifted too much
  if (gyroXangle < -180 || gyroXangle > 180)
    gyroXangle = kalAngleX;


  currAngle = compAngleX;

  //currAngle = kalAngleX;
  //int elim = (currAngle - prevAngle);
  //if (elim > 75 || elim < -75){
  // Serial.println("Fault!");
  // currAngle = prevAngle;//while(1);
  //}


  prevAngle = currAngle;
#ifdef BT_CONN
  Serial1.print(roll); Serial1.print(",");
  Serial1.print(gyroXangle); Serial1.print(",");
  Serial1.print(compAngleX); Serial1.print(",");
  Serial1.println(kalAngleX);
#endif
}


//PID Loop for Motor Speed control based on angle
void updateSpeed() {


  float K = 1;
  currError = targetAngle - currAngle;
  int errCheck = (currError - prevError);
  //Serial.print(currError);
  //Serial.print("   ");
  //Serial.print(prevError);
  //Serial.print("   ");
  //Serial.println(errCheck);
  if (abs(errCheck) > 20) {
    updateAngle();
    updateAngle();
    updateAngle();
    updateAngle();
    currError = targetAngle - currAngle;
    errCheck = (currError - prevError);

  }

  currError = constrain(currError, -75, 75);
  //Serial.println(currError);
  pTerm = Kp * currError;
  errorSum += currError;
  errorSum = constrain(errorSum, -200, 200);
  //Serial.println(errorSum);
  iTerm = Ki * errorSum;
  dTerm = Kd * (currError - prevError);
  prevError = currError;

  pT = Lp * returnto;
  dT = Ld * (returnto - prevE);
  prevE = returnto;
  //Serial.println(errorSum);


  if (fallflag == 1) {
    if (currError < 2 && currError > -2
       ) {
      fallflag = 0;
    }
  }

  if (currError > 60 || currError < -60) {
    stop();
    motorSpeed = 0;
    fallflag = 1;
    //    myEncA.write(0);
    myEncB.write(0);
  }
  else {
    if (fallflag == 0) {
      motorSpeed = constrain(K * (pTerm + iTerm + dTerm + pT + dT), -255, 255);
      //motorSpeed = constrain(K*(pTerm + iTerm + dTerm), -255, 255);
    }
  }
  //Serial.println(motorSpeed);

}


void updateMotor() {
  ///////Dont need now with encoders////////////////
  if (motorSpeed < 0) {
    dir = 1;
  }
  else if (motorSpeed > 0) {
    dir = 0;
  }

  if (motorSpeed < 0) {
    motorSpeed = motorSpeed * -1;
  }

  move(1, motorSpeed, dir, rotate);
  move(2, motorSpeed, dir, rotate);
  if (motorSpeed == 0) {
    stop();
  }
}


void move(int motor, int speed, int direction, float turn) {
  //Move specific motor at speed and direction
  //motor: 0 for B 1 for A
  //speed: 0 is off, and 255 is full speed
  //direction: 0 clockwise, 1 counter-clockwise


  int leftspeed, rightspeed;
  leftspeed = constrain((speed - (turn * turnREn)) , 0, 255);
  rightspeed = constrain((speed - (turn * turnLEn)) , 0, 255);


  boolean inPin1 = LOW;
  boolean inPin2 = HIGH;

  if (direction == 1) {
    inPin1 = HIGH;
    inPin2 = LOW;
  }
  /*if (lastdir != direction){
    stop();
    }
    lastdir = direction;
  */

  if (motor == 1) {
    digitalWrite(AIN1, inPin1);
    analogWrite(PWMA, leftspeed);
  }
  else {
    digitalWrite(BIN1, inPin1);
    analogWrite(PWMB, rightspeed);
  }
}
//Turns motors off.
void stop() {
  //Enable Standby
  analogWrite(PWMA, 0);
  analogWrite(PWMB, 0);

}

//Determines distance from target and sets an angle to make robot return to position.
void updateLocation() {
  //returnto = newPosition / 10;
  long AE, BE = 0;
  //  AE = myEncA.read();
  BE = myEncB.read();

  BE = BE * -1;
  if (BE > 400) {
    myEncB.write(-400);
  }
  //  if (AE > 400) {
  //    myEncA.write(400);
  //  }
  if (BE < -400) {
    myEncB.write(400);
  }
  //  if (AE < -400) {
  //    myEncA.write(-400);
  //  }
  //Serial.print(AE);
  //Serial.print(", ");
  //Serial.println(BE);
  offsetLoc = BE;
  //offsetLoc = (returnto + Movement) / 10 ;
  pT = Lp * offsetLoc;
  //errorS += offsetLoc;
  //errorS = constrain(errorS, -200, 200);
  //Serial.println(errorS);
  //iT = Li * errorS;
  dT = Ld * (offsetLoc - prevE);
  prevE = offsetLoc;
  correction = constrain(pT + dT, -4, 4);

}


char dataIn = 'S';
int repeat = 1;


/*///BLUETOOTH USE - NOT NEEDED
  void checkSerial(){
  char determinant;

  char lastData;
  int Movespeed = 7;
  float incrementAmt = 10;
  float maxDist = 100;


  if (Serial1.available() > 0)    //Check for data on the serial lines.
  {
    dataIn = Serial1.read();  //Get the character sent by the phone and store it in 'dataIn'.

    if (dataIn == 'S' || dataIn == 'F' || dataIn == 'B' || dataIn == 'L' || dataIn == 'R' || dataIn == 'I' || dataIn == 'J' || dataIn == 'G' || dataIn == 'H' ) {
      //Serial.println(dataIn);
      if (dataIn != 'S') {
        //myEncA.write(0);
        //myEncB.write(0);
      }
      if (dataIn == 'F')
      {
        determinant = 'F';

        if (Movement < maxDist) {
          Movement += incrementAmt;
        }
        rotate  = 0;

      }
      else if (dataIn == 'B')
      {
        determinant = 'B';
        //drive = Movespeed * -1;
        //correction = correction - 0.01;
        if (Movement > maxDist * -1) {
          Movement += incrementAmt * -1;
        }
        rotate  = 0;
      }
      else if (dataIn == 'L')
      {
        determinant = 'L';
        rotate = 20;
        turnLEn = 1;
        turnREn = -1;
      }
      else if (dataIn == 'R')
      {
        determinant = 'R';
        rotate = 20;
        turnREn = 1;
        turnLEn = -1;
      }
      else if (dataIn == 'I')
      {
        determinant = 'I';

        if (Movement < maxDist) {
          Movement += incrementAmt;
        }

        rotate = 20;
        turnREn = 1;
        turnLEn = -1;
      }
      else if (dataIn == 'J')
      {
        determinant = 'J';

        if (Movement > maxDist * -1) {
          Movement += incrementAmt * -1;
        }
        rotate = 20;
        turnREn = 1;
        turnLEn = -1;

      }
      else if (dataIn == 'G')
      {
        determinant = 'G';

        if (Movement < maxDist) {
          Movement += incrementAmt;
        }

        rotate = 20;
        turnLEn = 1;
        turnREn = -1;
      }
      else if (dataIn == 'H')
      {
        determinant = 'H';

        if (Movement > maxDist * -1) {
          Movement += incrementAmt * - 1;
        }
        rotate = 20;
        turnLEn = 1;
        turnREn = -1;
      }
      else if (dataIn == 'S')
      {

        //Serial.println(repeat);
        repeat = 1;
        if (Movement > 0) {
          Movement = Movement - 1;
        }
        determinant = 'S';
        //drive = 0;
        rotate = 0;
        //returnto = 0;
        correctionEn = 1;
        turnLEn = 0;
        turnREn = 0;
      }

      if (lastData != dataIn)
        repeat = 0;

      lastData = dataIn;

    }

  }




  }
*/

///Check the battery voltage, and stop system running if low.
void checkBatt() {
  int voltage = 0;
  voltage = analogRead(BATT);



  //Serial.println(voltage);
  if (voltage < 200) {
    Serial.println("Recharge Battery");
    while (1) {
      digitalWrite(17, HIGH);
      delay(500);
      digitalWrite(17, LOW);
      delay(500);
    }
  }
}


//If all POTs set to Zero, set the current angle to target angle. This will allow user to change the taget angle for better balancing.
void checkPots() {
  int P1, P2, P3 = 0;
  int pT = 50;
  int zeroed = 0;
  P1 = analogRead(pot1);
  P2 = analogRead(pot2);
  P3 = analogRead(pot3);
  while ((P1 < pT) && (P2 < pT) && (P3 < pT)) {
    updateAngle();
    tAngle = currAngle;
    P1 = analogRead(pot1);
    P2 = analogRead(pot2);
    P3 = analogRead(pot3);
    zeroed = 1;
  }
  saveAngle = tAngle * -1;
  if (zeroed == 1) {
    uint8_t tempAngle = EEPROM.read(1);
    if (tempAngle != saveAngle) {
      EEPROM.write(1, saveAngle);
      Serial.println("Saving to EEPROM");
    }
    zeroed = 0;
  }

}
/*
  void PIDtune(){


  if (Serial1.available() > 0) {   //Check for data on the serial lines.

    dataIn = Serial1.read();  //Get the character sent by the phone and store it in 'dataIn'.

    if (dataIn == 'P')
    {
      Lp += 0.01;
      Serial1.println(Lp);
    }


    else if (dataIn == 'L')
    {
      Lp += -0.01;
      Serial1.println(Lp);
    }
    else if (dataIn == 'I')
    {
      Li += 0.01;
      Serial1.println(Li);
    }
    else if (dataIn == 'J')
    {
      Li += -0.01;
      Serial1.println(Li);
    }
    else if (dataIn == 'D')
    {
      Ld += 0.01;
      Serial1.println(Ld);
    }
    else if (dataIn == 'X')
    {
      Ld += -0.01;
      Serial1.println(Ld);
    }
  }
  }
*/
////Test Motor RPM in relation to PWM.
void testMotors() {
  {
    //while (!Serial);
    int rpm, changeA, changeB = 0;


    //Serial.println(x);
    //    myEncA.write(0);
    myEncB.write(0);
    while (1) {
      move(1, 50, 1, 1);
      move(2, 50, 1, 1);
      delay(1000);
      move(1, 50, 0, 1);
      move(2, 50, 0, 1);
      delay(1000);
      move(1, 150, 1, 1);
      move(2, 150, 1, 1);
      delay(1000);
      move(1, 150, 0, 1);
      move(2, 150, 0, 1);
      delay(1000);

      move(1, 0, 0, 1);
      move(2, 0, 0, 1);
      delay(1000);
    }
    while (1) {
      //      changeA = myEncA.read();
      changeB = myEncB.read();
      Serial.print(changeA);
      Serial.print(", ");
      Serial.println(changeB);
      if (changeB > 1000) {
        move(B, 50, 0, 1);
      }
      if (changeA < -1000) {
        move(A, 50, 0, 1);

      }

      if (changeB < -1000) {
        move(B, 50, 1, 1);

      }
      if (changeA > 1000) {
        move(A, 50, 1, 1);

      }
    }
    delay(200);
    //rpm = ((change * 5 * 60) / 12) / 50;
    //Serial.println(rpm);

  }

}



void KalmanInit() {
  TWBR = ((F_CPU / 400000L) - 8) / 2; // Set I2C frequency to 400kHz

  i2cData[0] = 7; // Set the sample rate to 1000Hz - 8kHz/(7+1) = 1000Hz
  i2cData[1] = 0x00; // Disable FSYNC and set 260 Hz Acc filtering, 256 Hz Gyro filtering, 8 KHz sampling
  i2cData[2] = 0x00; // Set Gyro Full Scale Range to ±250deg/s
  i2cData[3] = 0x00; // Set Accelerometer Full Scale Range to ±2g
  while (i2cWrite(0x19, i2cData, 4, false)); // Write to all four registers at once
  while (i2cWrite(0x6B, 0x01, true)); // PLL with X axis gyroscope reference and disable sleep mode

  while (i2cRead(0x75, i2cData, 1));
  if (i2cData[0] != 0x68) { // Read "WHO_AM_I" register
    Serial.print(F("Error reading sensor"));
    while (1);
  }

  delay(100); // Wait for sensor to stabilize

  /* Set kalman and gyro starting angle */
  while (i2cRead(0x3B, i2cData, 6));
  accX = (i2cData[0] << 8) | i2cData[1];
  accY = (i2cData[2] << 8) | i2cData[3];
  accZ = (i2cData[4] << 8) | i2cData[5];

  // Source: http://www.freescale.com/files/sensors/doc/app_note/AN3461.pdf eq. 25 and eq. 26
  // atan2 outputs the value of -π to π (radians) - see http://en.wikipedia.org/wiki/Atan2
  // It is then converted from radians to degrees
#ifdef RESTRICT_PITCH // Eq. 25 and 26
  double roll  = atan2(accY, accZ) * RAD_TO_DEG;
  //double pitch = atan(-accX / sqrt(accY * accY + accZ * accZ)) * RAD_TO_DEG;

#endif

  kalmanX.setAngle(roll); // Set starting angle

  gyroXangle = roll;
  compAngleX = roll;

  timer = micros();
}

const uint8_t IMUAddress = 0x68; // AD0 is logic low on the PCB
const uint16_t I2C_TIMEOUT = 1000; // Used to check for errors in I2C communication

uint8_t i2cWrite(uint8_t registerAddress, uint8_t data, bool sendStop) {
  return i2cWrite(registerAddress, &data, 1, sendStop); // Returns 0 on success
}

uint8_t i2cWrite(uint8_t registerAddress, uint8_t *data, uint8_t length, bool sendStop) {
  Wire.beginTransmission(IMUAddress);
  Wire.write(registerAddress);
  Wire.write(data, length);
  uint8_t rcode = Wire.endTransmission(sendStop); // Returns 0 on success
  if (rcode) {
    Serial.print(F("i2cWrite failed: "));
    Serial.println(rcode);
  }
  return rcode; // See: http://arduino.cc/en/Reference/WireEndTransmission
}

uint8_t i2cRead(uint8_t registerAddress, uint8_t *data, uint8_t nbytes) {
  uint32_t timeOutTimer;
  Wire.beginTransmission(IMUAddress);
  Wire.write(registerAddress);
  uint8_t rcode = Wire.endTransmission(false); // Don't release the bus
  if (rcode) {
    Serial.print(F("i2cRead failed: "));
    Serial.println(rcode);
    return rcode; // See: http://arduino.cc/en/Reference/WireEndTransmission
  }
  Wire.requestFrom(IMUAddress, nbytes, (uint8_t)true); // Send a repeated start and then release the bus after reading
  for (uint8_t i = 0; i < nbytes; i++) {
    if (Wire.available())
      data[i] = Wire.read();
    else {
      timeOutTimer = micros();
      while (((micros() - timeOutTimer) < I2C_TIMEOUT) && !Wire.available());
      if (Wire.available())
        data[i] = Wire.read();
      else {
        Serial.println(F("i2cRead timeout"));
        return 5; // This error value is not already taken by endTransmission
      }
    }
  }
  return 0; // Success
}

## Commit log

2017-09-17 updated body
    [PIDDYBody_small_motor_lightweight.stl]
2017-09-21 added updated BOM
    [PIDDYBOT_32U4_BOM.csv]
2017-10-09 Added function demo
    [PIDDYBOT_V1_32U4.brd, PIDDYBOT_V1_32U4.sch]

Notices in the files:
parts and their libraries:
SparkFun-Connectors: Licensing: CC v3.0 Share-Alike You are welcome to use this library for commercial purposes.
